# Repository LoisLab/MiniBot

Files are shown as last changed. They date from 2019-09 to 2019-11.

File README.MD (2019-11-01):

# LoisLab AI Robotics Design & Construction
This repo has plans & software for the LoisLab MiniBot. The MiniBot is a tiny sensor-free rover, controlled by commands issued using http over a local-area network. Onboard the MiniBot, a RaspberryPi/Zero-W receives and executes commands by listening on port 80.

For example, if a MiniBot were logged into a wifi router at local address 192.168.0.103, accessing the following URLs would cause the MiniBot to execute various actions (like moving forward or turning):

<code>192.168.0.103/action=0</code><br>
<code>192.168.0.103/action=1</code><br>
<code>192.168.0.103/action=2</code><br>
<code>192.168.0.103/action=3</code><br>
<code>192.168.0.103/action=4</code><br>
<code>192.168.0.103/action=5</code><br>
<code>192.168.0.103/action=6</code><br>
<code>192.168.0.103/action=7</code><br>
<code>192.168.0.103/speed=0.40</code><br>

To start the robot's web service, access to pi via ssh and use: <code>sudo python3 start_webbot.py</code>.

A companion library uses OpenCV to observe one or more MiniBots, and attempt code challenges, like playing capture the flag.

Please read the included pdf, "Assembling the Mini Bot", for guidance on putting one together.

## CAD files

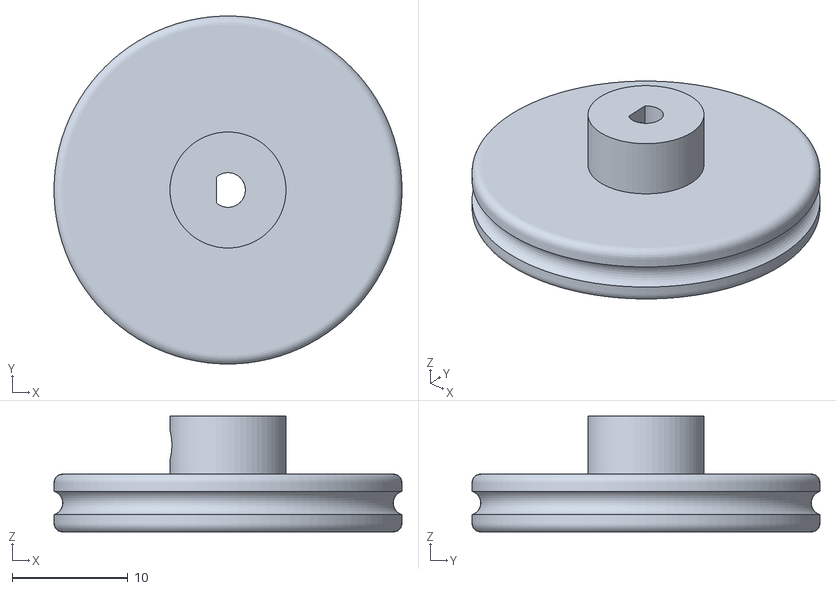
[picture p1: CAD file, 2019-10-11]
STLs/Wheel.stl
30.0 x 30.0 x 10.0

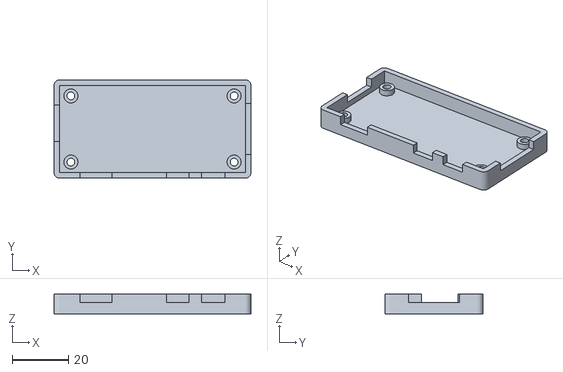
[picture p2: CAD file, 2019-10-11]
STLs/Pi_carrier.stl
70.0 x 35.0 x 7.00

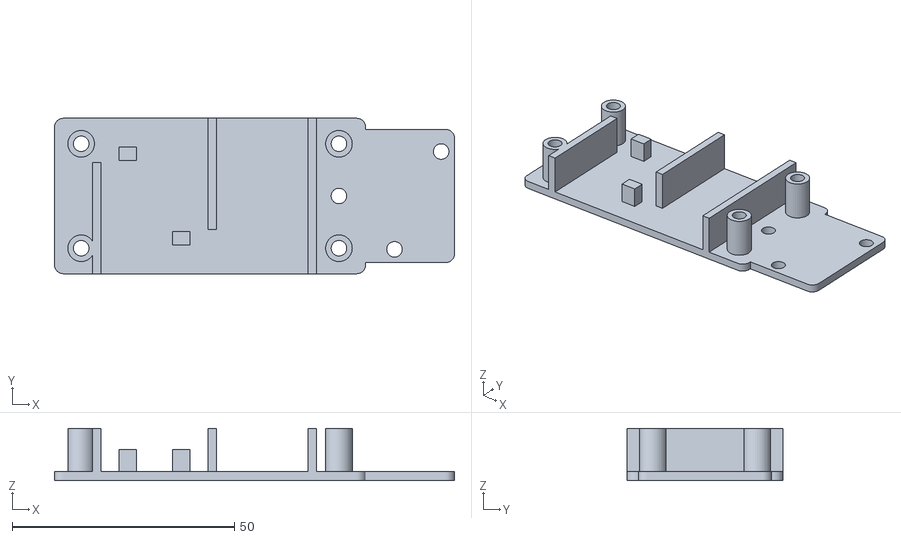
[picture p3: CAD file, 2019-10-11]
STLs/Motor_carrier.stl
90.0 x 35.0 x 11.7

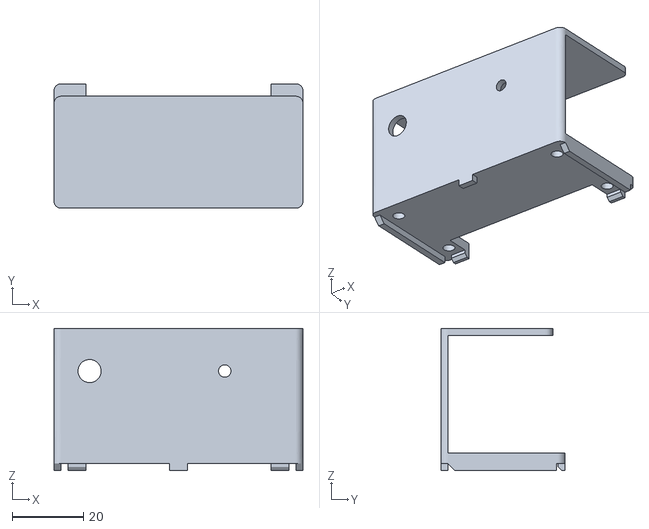
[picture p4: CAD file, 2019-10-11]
STLs/hbridge_carrier.stl
70.0 x 35.0 x 40.0

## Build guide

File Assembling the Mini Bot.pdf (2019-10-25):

# LoisLab

### MiniBot assembly guide

Here’s a quick run-through of the assembly process for the MiniBot (aka ‘Bob’). This isn’t a exhaustive step-by-step guide, but it should provide you with the details you need to put one together. As always, you can reach us at jeff@loislab.org or michael@loislab.org if you get stuck.

Here are the parts:

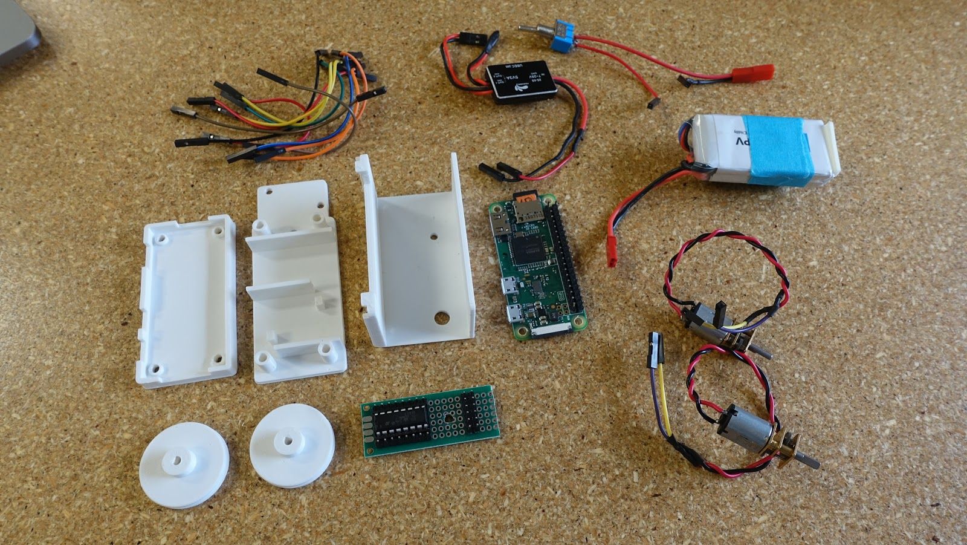
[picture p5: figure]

Bill of Materials

Item | Source
3D printed plastic parts (see below) | print them!
A Raspberry Pi Zero W | Adafruit, Micro Center
A 5v battery elimination circuit (BEC) from an RC vehicle Amazon ~ $5
An assortment of short female-to-female dupont wires | Amazon
Two N20-size DC motors, 12v/200rpm or so | Amazon, Aliexpress
A small (250-1000 mAH) 2-cell 7.4v lipo battery | Amazon, Hobbyking
M3 hardware | Amazon, local hardware store
(4) M3x25mm bolts
(1) M3x14mm bolt
(1) M3x8mm bolt
(7) M3 nuts
Toggle switch for a 6mm mounting hole | Amazon

Motor controller board, made from:
2cmx8cm protoboard | Amazon
L293D H-bridge chip | Adafruit, Amazon
Header pins
8-pin DIP chip socket
Assorted wires, solder, soldering iron, drill | Beg, borrow, don’t steal

Download and print the white plastic parts - you can find them on our github as part of the MiniBot repo. (https://github.com/LoisLab/MiniBot) They’re in the STLs folder and are all printable without support material.

The Motor Controller

Before we assemble the robot, we need to construct the circuit board that holds the motor controller chip.

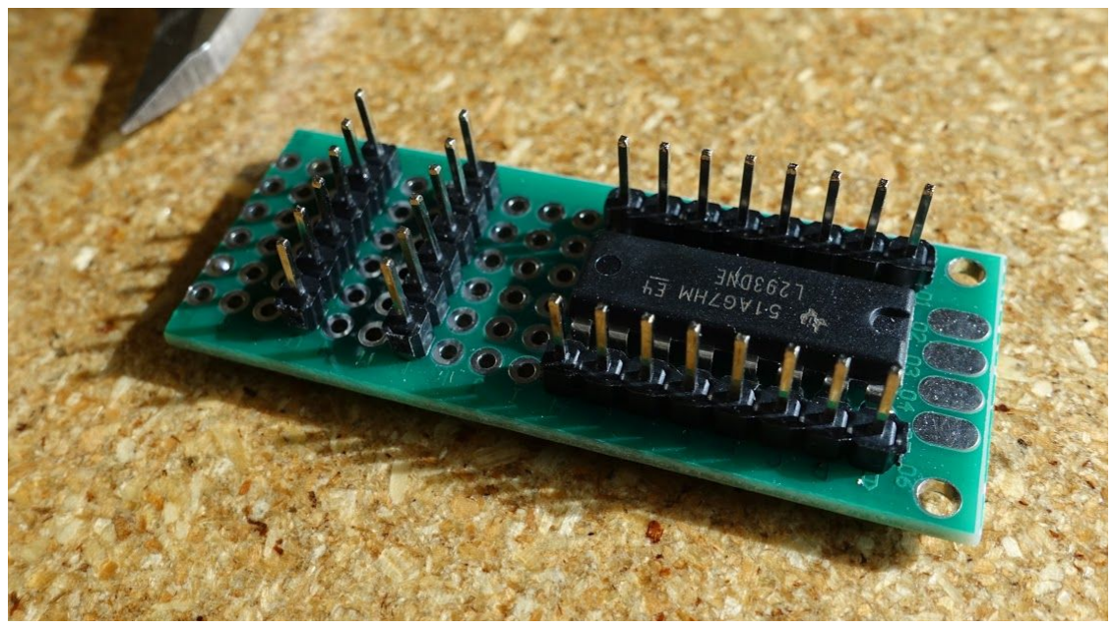
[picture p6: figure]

Start by scoring and snapping the protoboard to give you a piece that is 20mm wide and 50mm long:

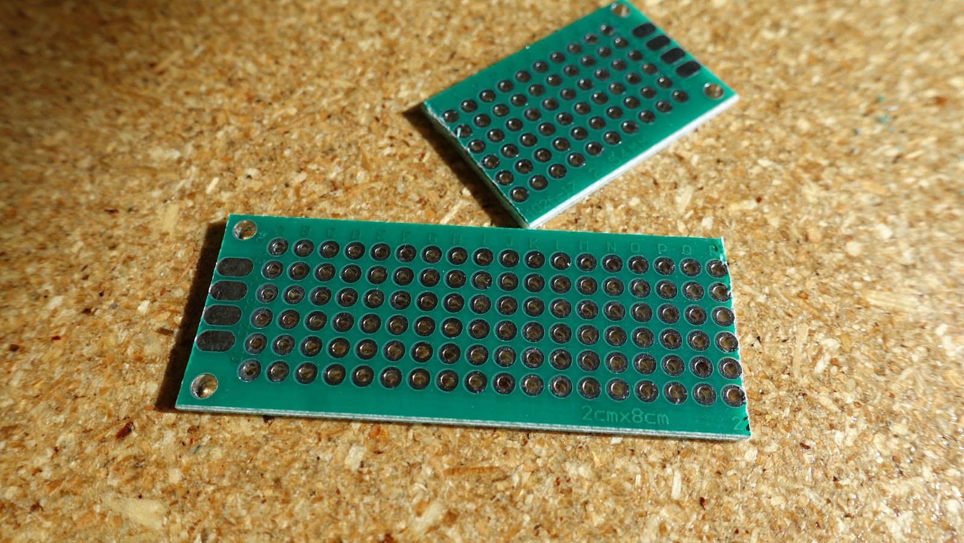
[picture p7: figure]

Line up the chip socket and pins, and use a piece of tape or your finger to hold them in place while you solder. Parts get hot, be careful.

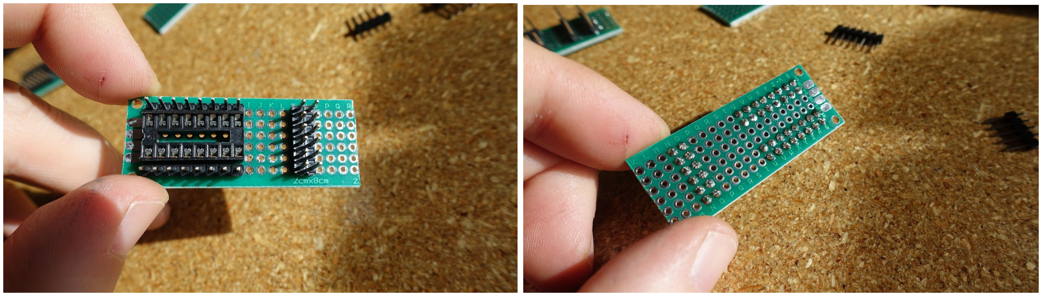
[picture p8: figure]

Once the pins are all soldered, carefully bridge each socket pin to the header pin next to it. If you’re not a confident solderer, or you have trouble, you can use a little piece of wire to make the connection and then solder that in place.

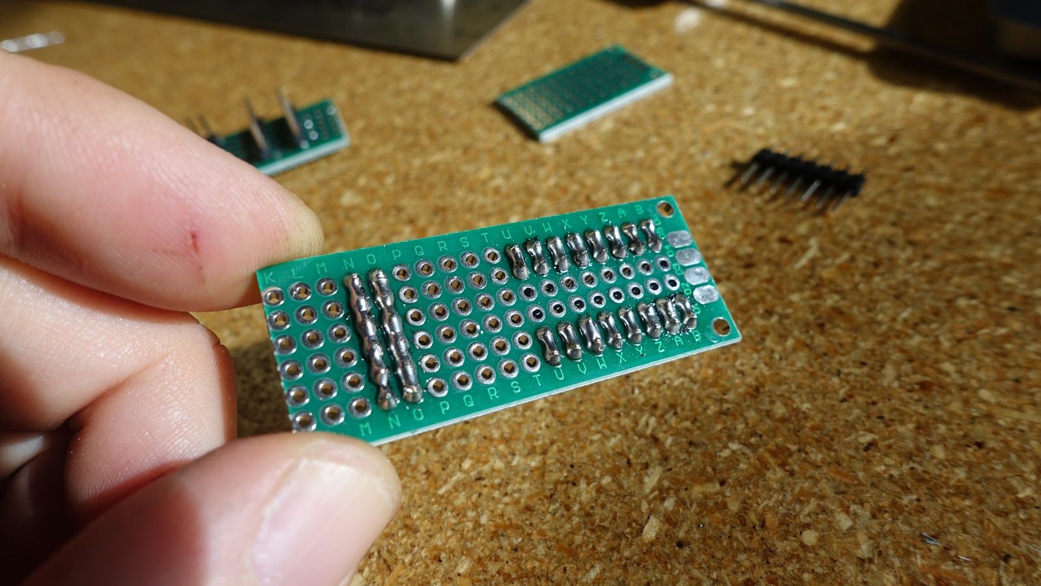
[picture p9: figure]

Gently press the chip in place. The marking for pin 1 (an indentation, on this chip) should be at the end of the board. Hold the board up to the U-shaped board carrier plastic part and mark where you want the mounting hold to go. The exact location isn’t critical, but I like to place the hole so the board will rest against one of the overhangs and be held in place as shown in the last photo.

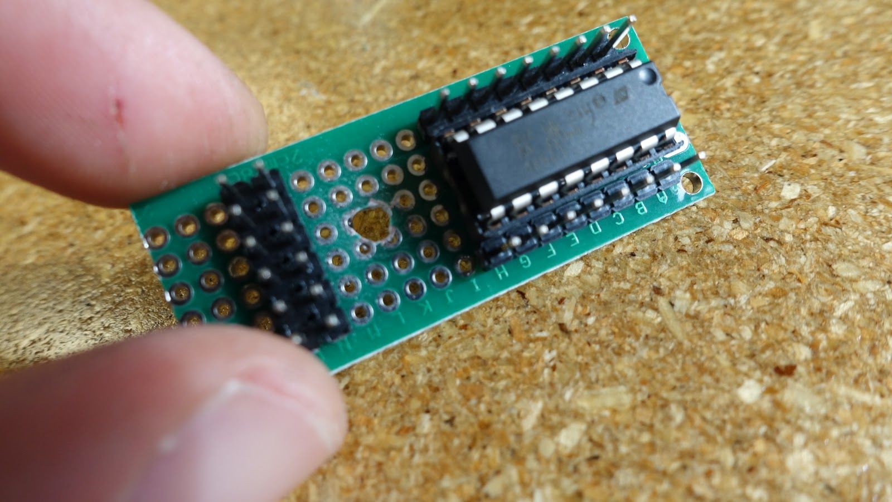
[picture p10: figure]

The board installed:

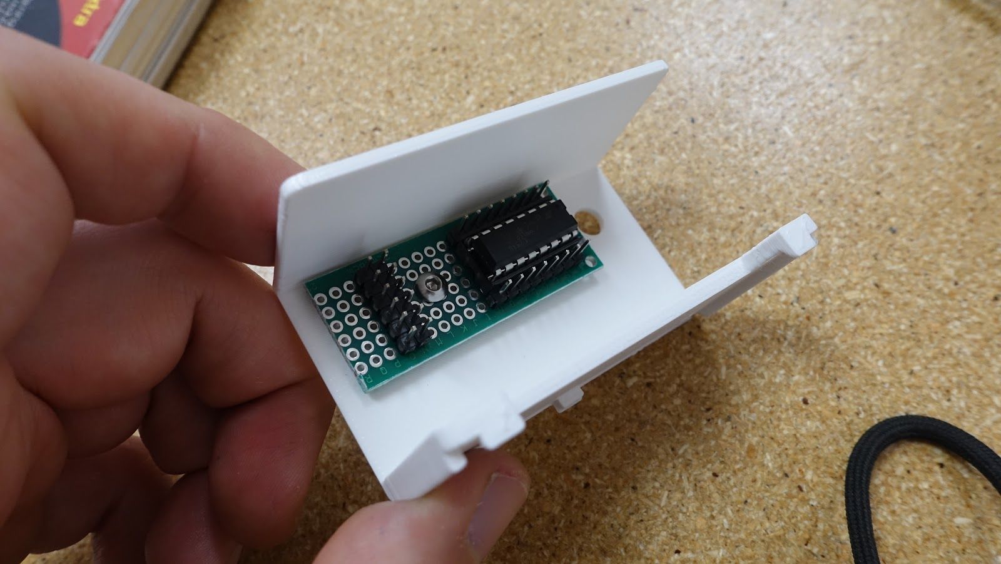
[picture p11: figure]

Assembling the MiniBot

The robot is essentially a sandwich of three sections that hold the motors and Raspberry Pi contained together.

Start by pressing the wheels onto the motor shafts. If it is difficult to get them started, make sure the openings are clear using pick or the tip of a hobby knife. You can heat the motor shafts gently with a soldering iron to deform the plastic around the shafts slightly, but be careful as too much heat might result in the wheels sitting off-axis and wobbling.

Cut a couple of the dupont wires and solder them onto the motors so you can plug them into the motor controller board. If the motors are marked with (+) or (-) terminals, you can get the colors to match between the motors when you solder the wires on; it might make your job easier later on.

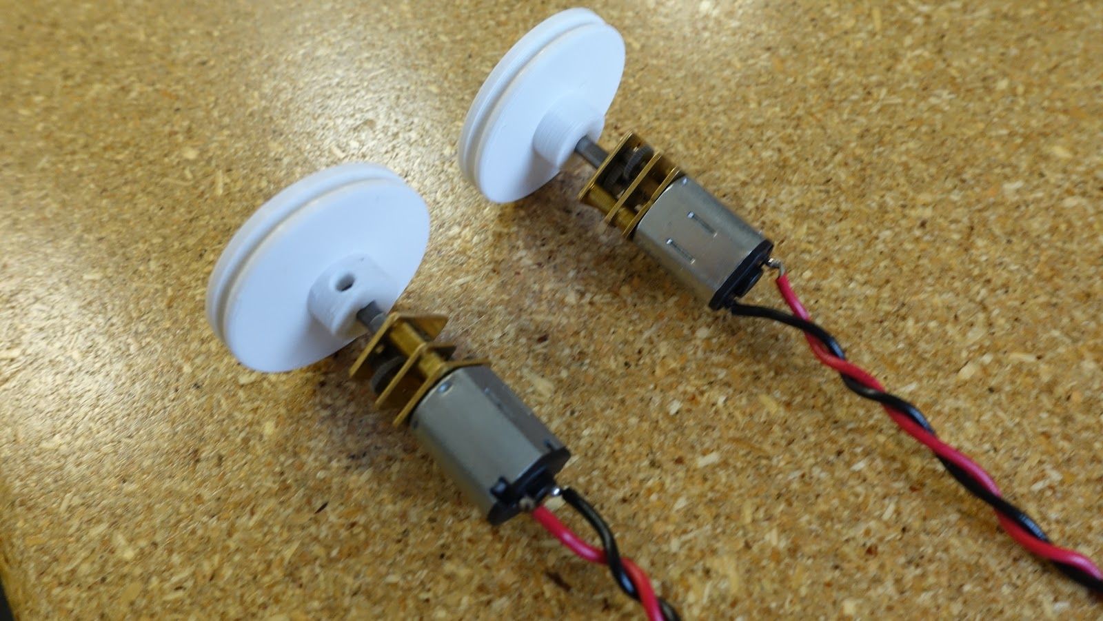
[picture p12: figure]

Set the motors in opposing directions in the motor carrier board. Retention pegs will rest against the rear of each motor to locate them properly; the gearbox plates should sit flush with the outer edge of the motor carrier part.

[PIC]

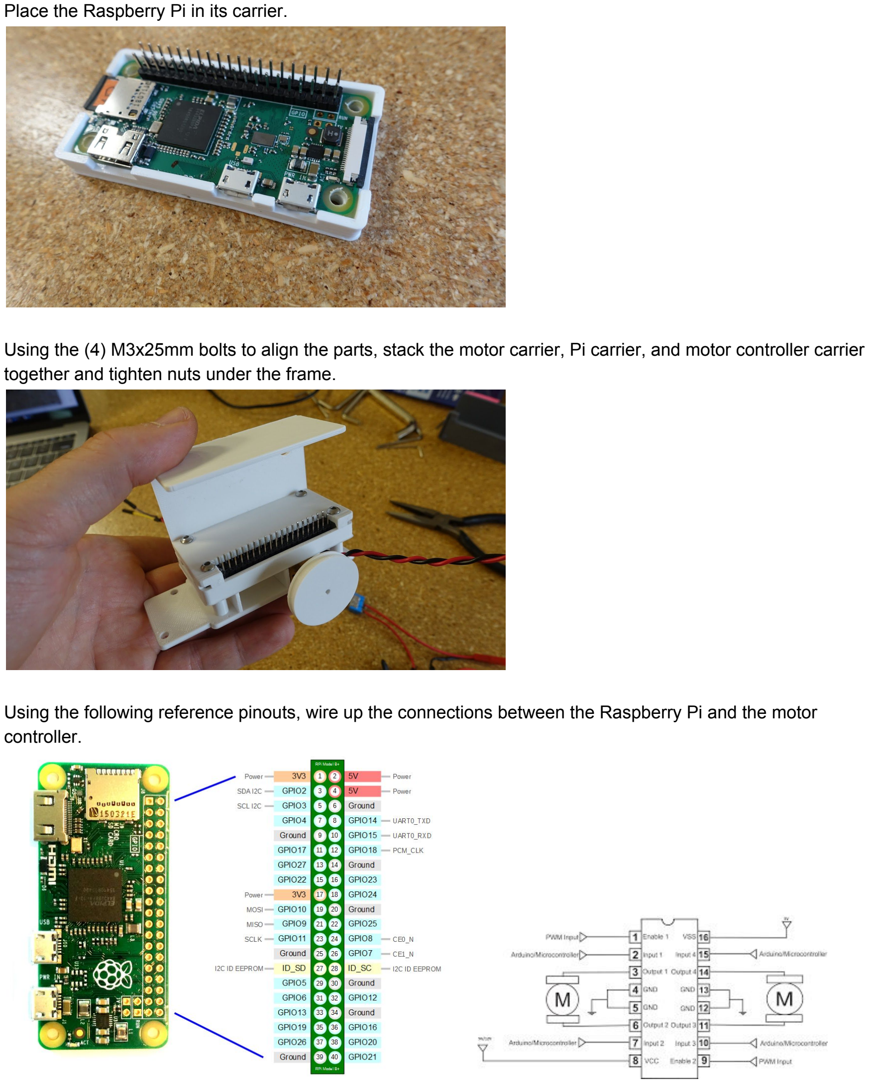
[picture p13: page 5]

Place the Raspberry Pi in its carrier.

Using the (4) M3x25mm bolts to align the parts, stack the motor carrier, Pi carrier, and motor controller carrier together and tighten nuts under the frame.

Using the following reference pinouts, wire up the connections between the Raspberry Pi and the motor controller.

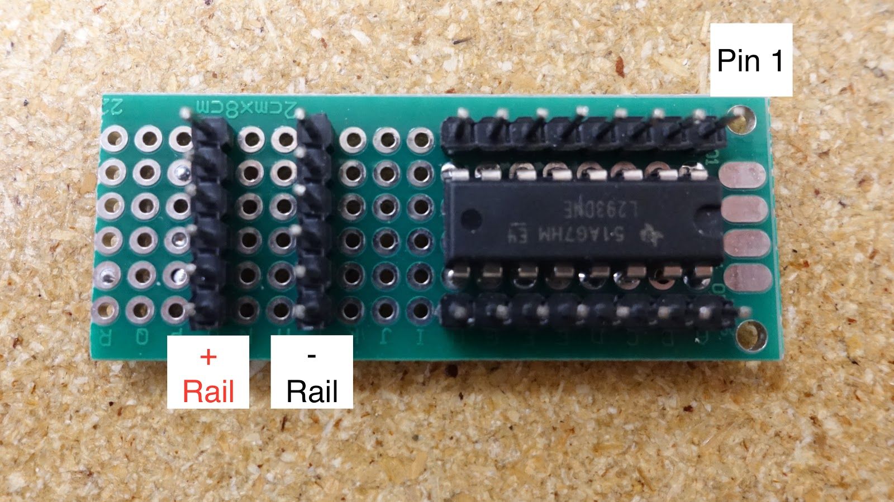
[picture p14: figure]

Motor driver pin | Connects to | Battery connector | Connects to
#1 | Pi pin 7 | 7.4v + | + rail

#2 | Pi pin 3 | 7.4v - | - rail

#3 | motor #1 (+)

#4 | - rail | BEC | Connects to

#5 | not connected | BEC + input | + rail

#6 | motor #1 (-) | BEC - input | - rail

#7 | Pi pin 5 | BEC output | Pi pin 4

#8 | + rail | BEC output | Pi pin 6

#9 | Pi pin 15

#10 | Pi pin 11

#11 | motor #2 (-)

#12 | - rail

#13 | not connected

#14 | motor #2 (+)

#15 | Pi pin 13

#16 | Pi pin 2

Optionally, you can wire the switch so it is between the LiPo + battery connection into the + power rail. This is a nice feature to keep the battery from running down when the robot is not in use.

Use a 14mm M3 bolt as the front ‘skid’ or third wheel. Put one nut on the bolt, slide it into the hole on the bottom of the chassis, and hold it in place with the other nut.

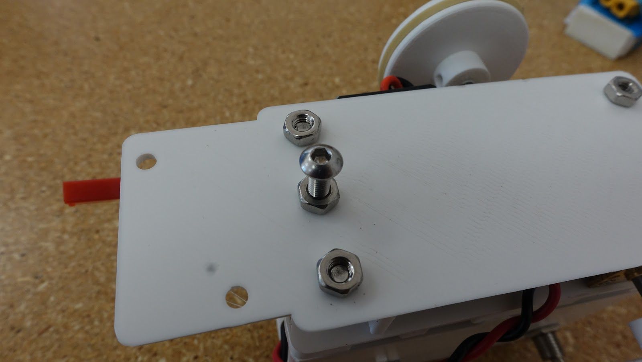
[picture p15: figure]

Here is the completed bot.

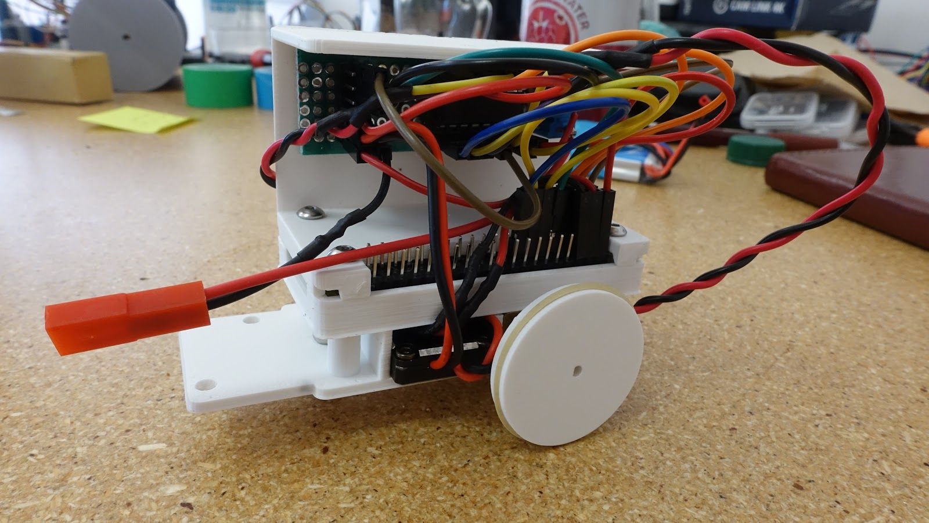
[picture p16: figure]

Configuring the software

Boot the Pi Zero W with the latest Raspbian image.

Clone the MiniBot software repo with the following command:

git clone https://github.com/LoisLab/MiniBot.git

Trying out the MiniBot

Log in to the Pi.

Go to the directory where you cloned the repo. In our case:

cd ~/MiniBot

Start up the web service that listens for commands:

sudo python3 webbot.py

You can now give the little robot commands using a web browser. For example, let’s say your robot is joined up to your wireless network and has an IP address of 192.168.0.199, you could make it move by putting the following URL in your browser:

http://192.168.0.199/action=0

The service accepts eight action commands (0-7). Have fun playing with it.

As always, you can reach us at jeff@loislab.org or michael@loislab.org if you get stuck, or just to tell us stories about how you’ve been using it.

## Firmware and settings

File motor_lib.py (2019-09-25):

import RPi.GPIO as GPIO
from time import sleep


class Motors:
    
    def __init__(self, left_pins=(3,5,7), right_pins=(11,13,15)):
        GPIO.setmode(GPIO.BOARD)
        self.left=Motor(left_pins)
        self.right=Motor(right_pins)
        
    def set_direction(self,left_dir,right_dir):
        self.left.set_direction(left_dir)
        self.right.set_direction(right_dir)
        
    def go(self):
        self.left.go()
        self.right.go()
        
    def stop(self):
        self.left.stop()
        self.right.stop()

    def cleanup(self):
        self.stop()
        GPIO.cleanup()


class Motor:
    
    FORWARD=(GPIO.HIGH,GPIO.LOW)
    REVERSE=(GPIO.LOW,GPIO.HIGH)
    
    def __init__(self, pins):
        self.pins=pins
        GPIO.setup(self.pins[0], GPIO.OUT)
        GPIO.setup(self.pins[1], GPIO.OUT)
        GPIO.setup(self.pins[2], GPIO.OUT)
        GPIO.output(self.pins[2], GPIO.LOW)

    def set_direction(self, direction):
        GPIO.output(self.pins[0], direction[0])
        GPIO.output(self.pins[1], direction[1])
        
    def go(self):
        GPIO.output(self.pins[2], GPIO.HIGH)
        
    def stop(self):
        GPIO.output(self.pins[2], GPIO.LOW)

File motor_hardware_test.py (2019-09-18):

import RPi.GPIO as GPIO
from time import sleep

GPIO.setmode(GPIO.BOARD)

#Motor 1 setup
GPIO.setup(3, GPIO.OUT)
GPIO.setup(5, GPIO.OUT)
GPIO.setup(7, GPIO.OUT)

#Motor 2 setup
GPIO.setup(11, GPIO.OUT)
GPIO.setup(13, GPIO.OUT)
GPIO.setup(15, GPIO.OUT)

#Set up the enable pins
pwm1=GPIO.PWM(7, 100)
pwm2=GPIO.PWM(15, 100)
pwm1.start(0)
pwm2.start(0)
pwm1.ChangeDutyCycle(100)
pwm2.ChangeDutyCycle(100)

#Motor 1 forward
GPIO.output(3, True)
GPIO.output(5, False)

#Motor 2 forward
GPIO.output(11, True)
GPIO.output(13, False)

#Enable both motors
GPIO.output(7, True)
GPIO.output(15, True)

sleep(2)

#Disable both motors
GPIO.output(7, False)
GPIO.output(15, False)

#Motor 1 reverse
GPIO.output(3, False)
GPIO.output(5, True)

#Motor 2 reverse
GPIO.output(11, False)
GPIO.output(13, True)

#Enable both motors
GPIO.output(7, True)
GPIO.output(15, True)

sleep(3)

#Shut everything off
GPIO.output(7, False)
GPIO.output(15, False)
pwm1.stop()
pwm2.stop()
GPIO.cleanup()
